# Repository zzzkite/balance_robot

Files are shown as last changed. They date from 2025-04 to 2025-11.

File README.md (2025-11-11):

# 轮腿机器人 - 毕设版

## PS2 操作说明

**注意：手柄信号可能不稳定，存在失控风险**

### 按键功能

- **失能按键**：`R2` (右上角第2个键)
  - 发送电机失能信号
  - 关节电机指示灯变为红色
  - 支持远程停止机器人

- **使能按键**：`start`
  - 发送电机使能信号  
  - 电机指示灯变为绿色

- **启动控制**：`L2` (左上角第二个键)
  - 需在电机使能后使用
  - 启动控制程序

- **跳跃功能**：`R1` (右上角第一个键)

- **前后移动**：右摇杆前后方向

- **左右旋转**：右摇杆左右方向

- **腿长变化**：左摇杆前后方向

- **横滚角控制**：左摇杆左右方向

## 项目文件架构
├── balance_robot_stm/ # STM32 主控代码
├── matlab/ # MATLAB 仿真文件
├── matlab results/ # 仿真视频和力矩数据
├── motor param/ # 关节电机参数存档
├── reference/ # 参考资料文档
├── Soildworks/ # 机械设计文件
│ ├── 3D模型/
│ ├── 打印件/
│ └── 机加工件/
├── test movie/ #实机测试视频
└── bom表/ # 物料清单

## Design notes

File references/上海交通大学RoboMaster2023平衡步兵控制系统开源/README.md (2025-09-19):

# 上海交通大学交龙战队平衡步兵控制系统开源说明文档

## 概述

本文档为上海交通大学交龙战队平衡步兵控制系统开源说明文档，给出了开源内容的索引和研发思路。本次开源的内容主要为控制系统的设计文档以及一些用于参考的测试视频。

本开源项目出自上海交通大学交龙战队，仅用于技术交流，未经作者允许，不得作任何商业用途。

转载需注明作品出处，对非法转载者，作者保留采用法律手段追究的权利。

## 索引

### 文档

1. 动力学模型-[WBR_control](WBR_control.html)
2. 腿部机构分析-[WBR_leg](WBR_leg.html)
3. 控制器设计-[WBR_control](WBR_control.html)

### 研发计划

1. 研发计划文档-[plan](plan.md)

### 手写稿

部分内容未整理成电子版，以手写稿形式开源，包括功率限制、自适应调节（防打滑策略）、陀螺平移等。此外建模分析和控制部分的电子稿在整理过程中可能有一些遗漏，手写稿也可作为一定参考。

1. 建模分析-[modelling](note/modelling/modeling_1.jpg)
2. 腿部机构分析-[leg](note/leg/leg_1.jpg)
3. 功率限制-[power](note/power/power_1.jpg)
4. 自适应调节-[predictor](note/predictor_and_controller.jpg)
5. 陀螺平移&腿部自重系数-[other](note/other.jpg)

### 控制系统框图

给出控制系统核心部分（运动控制-平衡、移动、旋转，腿部控制-高度、横滚）控制框图。系统由4部分组成：(1)目标状态输入，(2)控制器，(3)机器人模型，(4)观测器。

1. 系统框图-[system](assets/control_system/system.jpg)
2. 控制器-[controller](assets/control_system/controller.jpg)
3. 运动控制器-[locomotion_controller](assets/control_system/locomotion_controller.jpg)
4. 腿部控制器-[leg_controller](assets/control_system/leg_controller.jpg)
5. 观测器-[observer](assets/control_system/observer.jpg)

### 仿真

assets/sim_WBR_control 文件夹包含simulink仿真视频和仿真的状态曲线

### 测试视频

assets/test_video 文件夹中包含各项功能的测试视频，可作为运动性能和鲁棒性的参考。

## 硬件方案

- 驱动轮：3508电机+自制行星减速箱（14:1减速比）
- 关节电机：HT04
- 主控：STM32F407（C型开发板）
- IMU：BMI088（C板集成）

## 研发思路

我们的平衡步兵采用轮腿设计，轮腿结构在起伏路段、斜坡、横向移动等方面均有一定优势，相应的控制系统也相对复杂。考虑到模型的复杂性以及在单片机上运行的资源消耗等因素，采用LQR实现平衡运动控制。

2022赛季哈尔滨工程大学创梦之翼战队的平衡步兵在比赛中表现出了非常优秀的性能，赛季结束后他们也开源了平衡步兵的控制系统[1]。我们的控制系统在设计时一些处理参考了其思路。

此前轮腿机器人的模型多数简化为两级倒立摆[1][2][3]，对于两条腿的处理并不完善，同时轮电机的控制分为平衡移动和旋转两部分，不完全解耦。由此我们认为轮腿机器人在高速移动中的转向性能仍没有被完全发挥，因此在根据倒立摆模型初步验证了平衡控制算法后，重新建立了包含双腿的机器人全身动力学模型，并基于该模型设计了解耦的控制系统。

在完成核心的平衡、运动控制和腿部控制后，为了进一步提升平衡步兵在赛场上的性能和鲁棒性，我们又做了一系列优化和功能开发。

针对赛场上满地弹丸的场景设计了自适应调节器，设计该调节器的基本思路依然是希望控制输出解耦。相比根据额外的传感器判断是否踩到弹丸或轮子悬空，这种调节器不会破坏原有模型和控制系统的完整性，而是通过类似于轨迹跟踪的方式，仅在系统偏离模型的状态下介入，保证了系统的鲁棒性。

相比传统的四轮步兵，平衡车的功率限制相对难实现，也有采用超级电容+开环的做法，但一方面这样在电容没电时很容易超功率（赛场上不少队伍出现平衡卡墙后连续超功率的情况），另一方面也难以充分发挥平衡车的运动性能。平衡车功率限制的方式目前有两种：一种是采用NMPC控制，利用NMPC带约束优化的特性对功率进行限制（可参考广东工业大学DynamicX战队23赛季青工会答辩[4]），这种方式思路相对直观，但对计算平台算力要求很高；另一种方式是通过分析控制律，得到计算消耗非常低的功率限制条件，可在单片机上以1Khz运行。

由于平衡步兵无法实现全向移动，在赛场上操作存在许多制约。但在陀螺状态下，通过变速平衡车可以近似实现全向平移，这一功能在赛场上能有效提升平衡的机动性和生存能力。

最后，车的稳定性在比赛中尤为重要，平衡车具备在发生冲撞、下台阶、跳跃等情况时保持不翻，并在极短时间恢复平衡的能力才能支持操作手放心地完成各种操作。

## 参考资料

[1] [RoboMaster平衡步兵机器人控制系统设计](https://zhuanlan.zhihu.com/p/563048952)（哈尔滨工程大学创梦之翼战队，2022）  
[2] S. Wang et al., "Balance Control of a Novel Wheel-legged Robot: Design and Experiments," 2021 IEEE International Conference on Robotics and Automation (ICRA), 2021, pp. 6782-6788, doi: 10.1109/ICRA48506.2021.9561579.  
[3] V. Klemm et al., "Ascento: A Two-Wheeled Jumping Robot," 2019 International Conference on Robotics and Automation (ICRA), 2019, pp. 7515-7521, doi: 10.1109/ICRA.2019.8793792.  
[4] [RMUC 2023青工会技术答辩-广东工业大学-无下位机电控、平衡步兵模型预测控制](https://www.bilibili.com/video/BV18F41117QZ)

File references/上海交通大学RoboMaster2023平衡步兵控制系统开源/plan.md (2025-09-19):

# 轮腿平衡控制研发计划

## 1 基础平衡控制

固定腿长，平地直线运动，平衡控制基本原理验证

- [x] 动力学分析
- [x] 控制算法
- [x] 简化模型仿真验证
- [x] 腿部连杆运动学分析
- [x] 平衡+腿部控制仿真验证
- [ ] ~~非线性控制*~~

## 2 整体运动控制

实现基本的运动功能，优化运动性能

~~路线1~~

- [ ] 双腿协调
- [ ] 腿长控制
- [ ] 转向控制
- [ ] 横滚角

路线2（完整模型）

- [x] 全身动力学建模
- [x] 控制算法
- [x] 仿真验证

## 3 实际机器人控制

- [x] 无线调试器+串口测试
- [x] 陀螺仪校准
- [x] 线路连接设计
- [x] 关节电机驱动
- [x] 电机力控实现+验证
- [x] 腿部运动学验证
- [x] 控制算法实现
- [x] 测试

## 4 进阶功能

提升鲁棒性，实现一些进阶功能如跳跃、扰动自适应等。

- [x] 原地静止（尝试增大速度环系数+速度环输入限幅缩小+减小角度系数，效果不好则尝试力位混控）
- [x] 测试不同腿长起身效果，大角度状态缩短腿长
- [x] 扰动观测器
- [x] 打滑检测（观测器+力位混控）
- [x] 离地检测+落地（通过腿长PID输出可估计地面支持力，roll PID系数表示为腿长PID的函数）
- [x] 陀螺平移（偏心旋转，周期速度规划）
- [x] 主动跳跃（运动中跳跃/原地）
- [ ] 自动跳跃运动规划
- [x] 功率限制
- [x] 测试

## 5 整车

比赛用车整备至上场状态

硬件

- [x] 走线整理
- [x] 滑环焊线
- [x] 云台
- [x] 轮电机id+换线
- [x] minipc
- [x] 相机
- [x] 裁判系统
- [x] 电容
- [x] 继电器
- [x] 保护
- [x] 保养+备件

软件

- [x] 上板程序
- [x] 云台程序
- [x] 遥控器操作
- [x] 键鼠操作
- [x] 自瞄
- [x] 功率限制
- [ ] ui

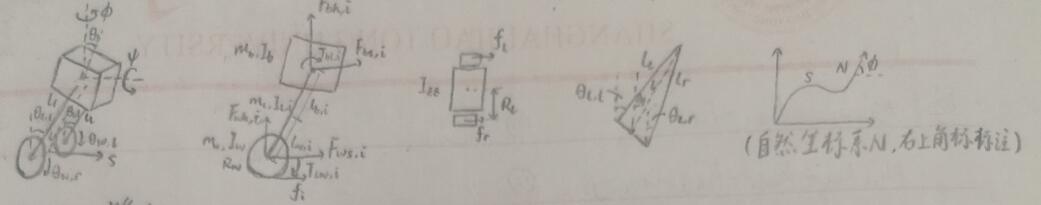
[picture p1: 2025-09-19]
references/上海交通大学RoboMaster2023平衡步兵控制系统开源/assets/figure/model.jpg

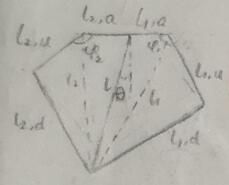
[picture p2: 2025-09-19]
references/上海交通大学RoboMaster2023平衡步兵控制系统开源/assets/figure/leg_1.jpg

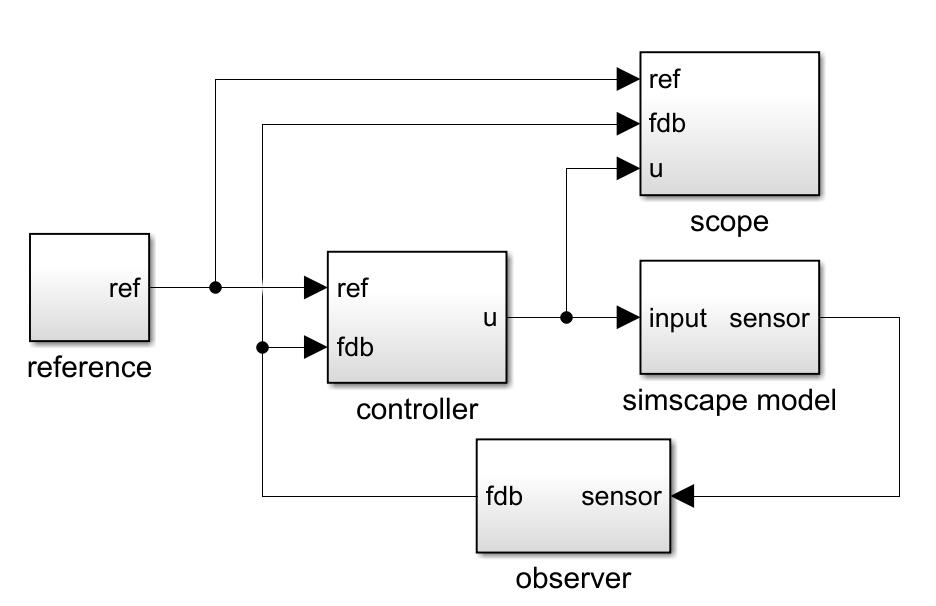
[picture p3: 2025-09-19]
references/上海交通大学RoboMaster2023平衡步兵控制系统开源/assets/control_system/system.jpg

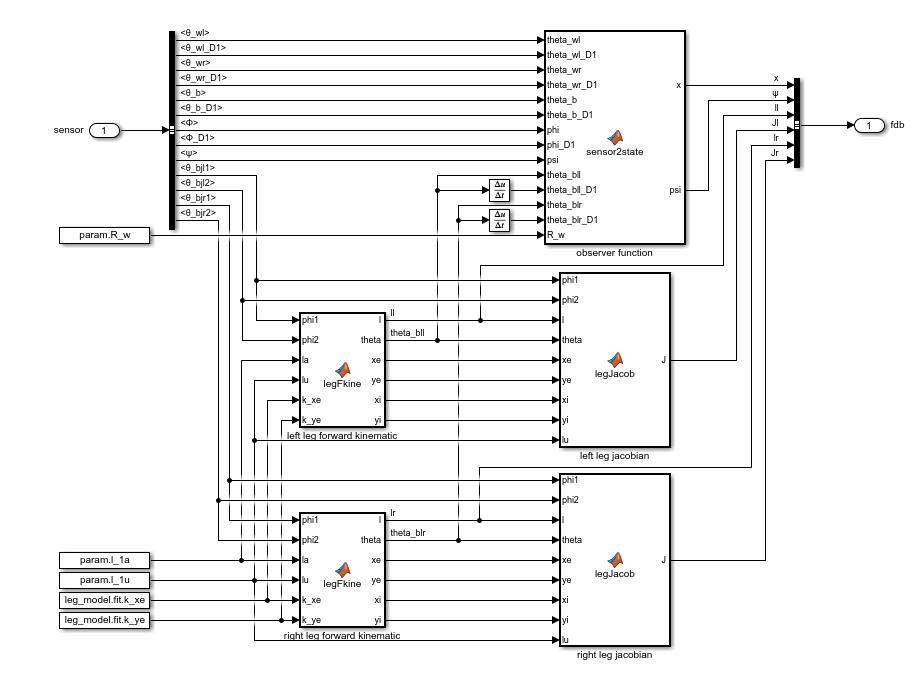
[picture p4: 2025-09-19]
references/上海交通大学RoboMaster2023平衡步兵控制系统开源/assets/control_system/observer.jpg

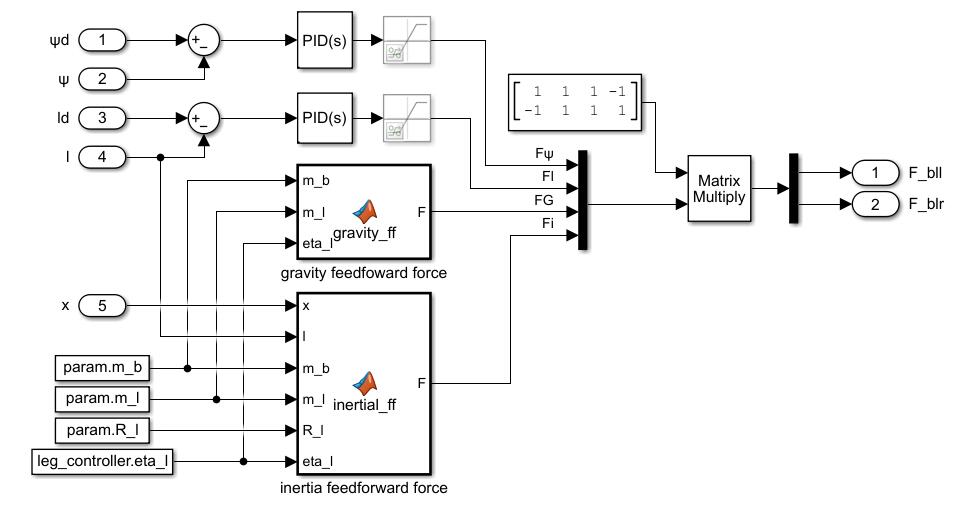
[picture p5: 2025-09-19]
references/上海交通大学RoboMaster2023平衡步兵控制系统开源/assets/control_system/leg_controller.jpg

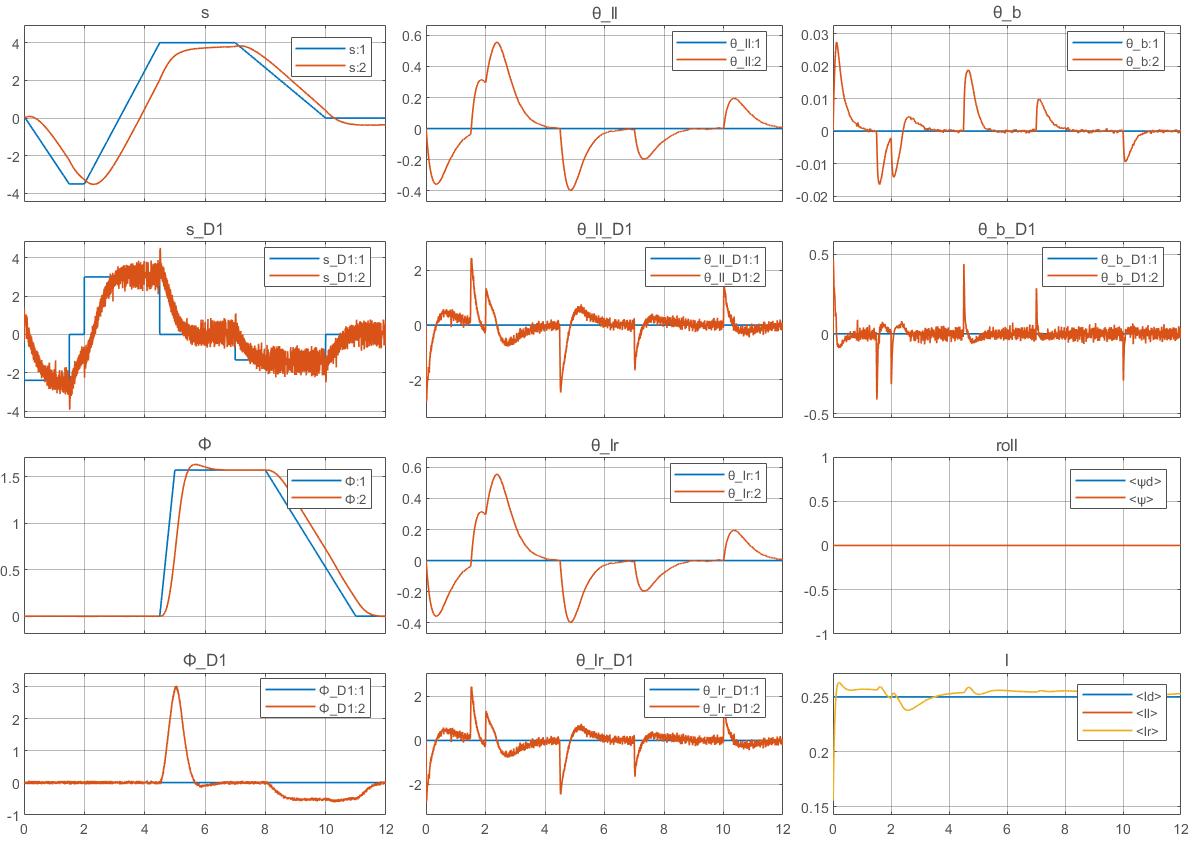
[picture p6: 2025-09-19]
references/上海交通大学RoboMaster2023平衡步兵控制系统开源/assets/sim_WBR_control/state.jpg

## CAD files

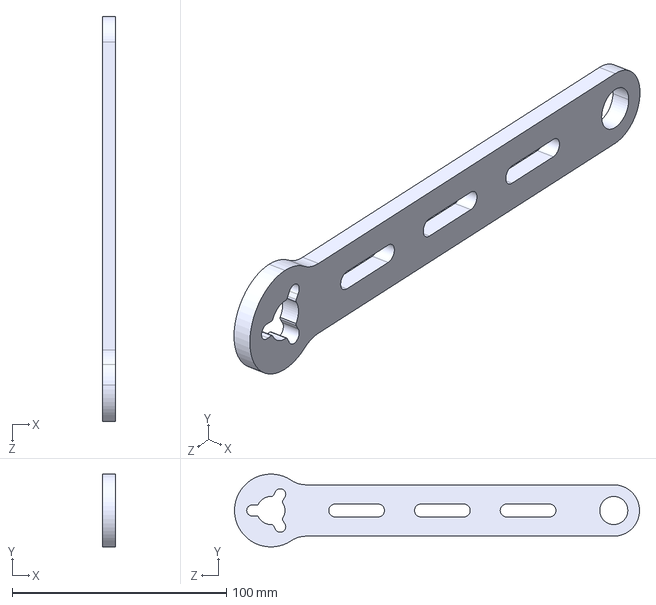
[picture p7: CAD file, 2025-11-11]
Soildworks/Version1.0-sw-加工件/加工连杆2.STEP
6.00 x 34.0 x 189.0 mm

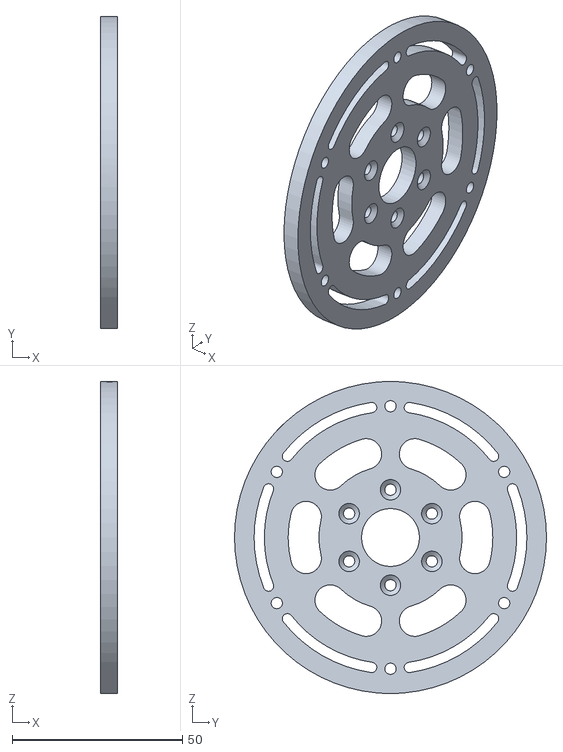
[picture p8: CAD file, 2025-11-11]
Soildworks/Version1.0-sw-打印件/轮毂打印件-上盖片.STL
5.00 x 91.5 x 91.5

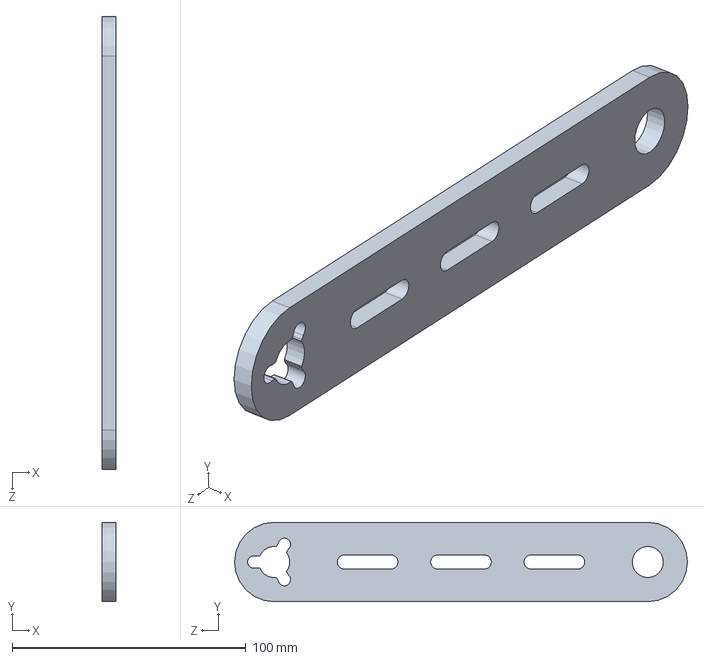
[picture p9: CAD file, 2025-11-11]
Soildworks/Version1.0-sw/连杆6.sldprt
6.00 x 34.0 x 194.0 mm

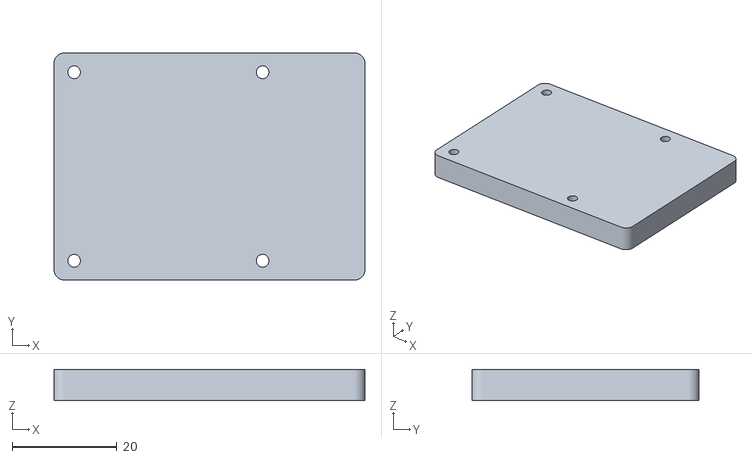
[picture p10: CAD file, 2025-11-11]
Soildworks/Version1.0-sw-打印件/stm32后壳.STL
59.4 x 43.4 x 6.00

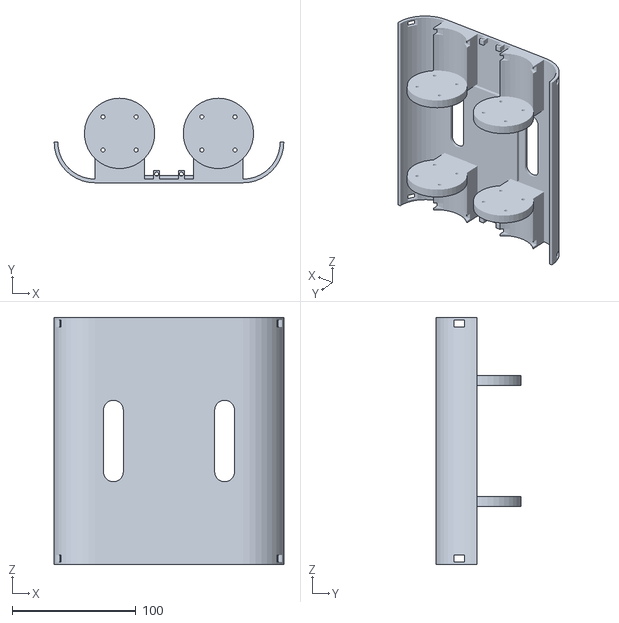
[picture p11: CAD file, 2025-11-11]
Soildworks/Version1.0-sw-打印件/机架底板.STL
186.0 x 68.5 x 200.0

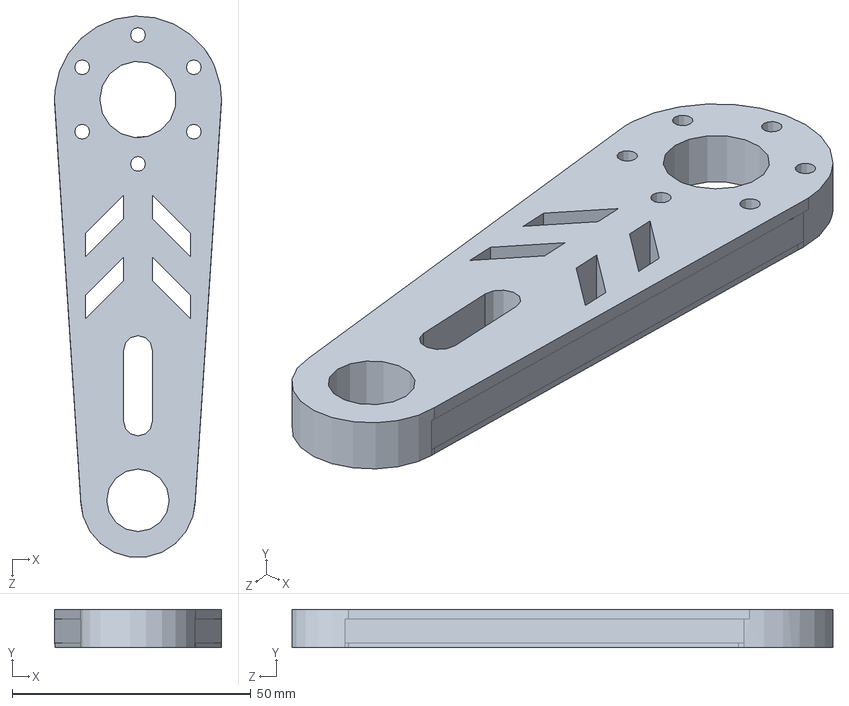
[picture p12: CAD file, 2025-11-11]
Soildworks/Version1.0-sw/加工连杆3.sldprt
35.0 x 8.00 x 113.4 mm

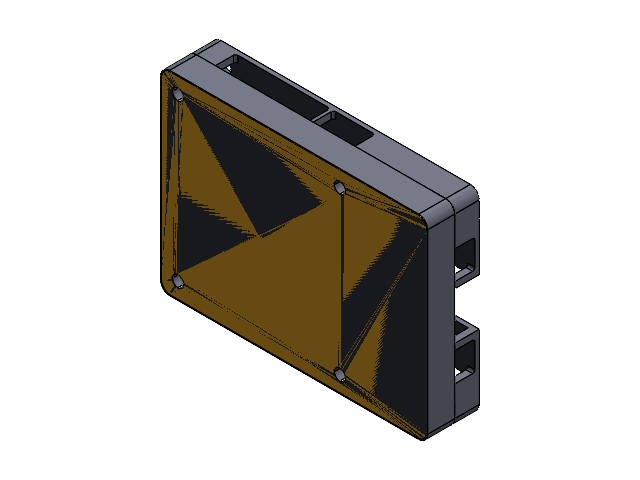
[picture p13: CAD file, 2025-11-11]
Soildworks/Version1.0-sw/stm32装配体.SLDASM
stm32后壳
stm32前壳

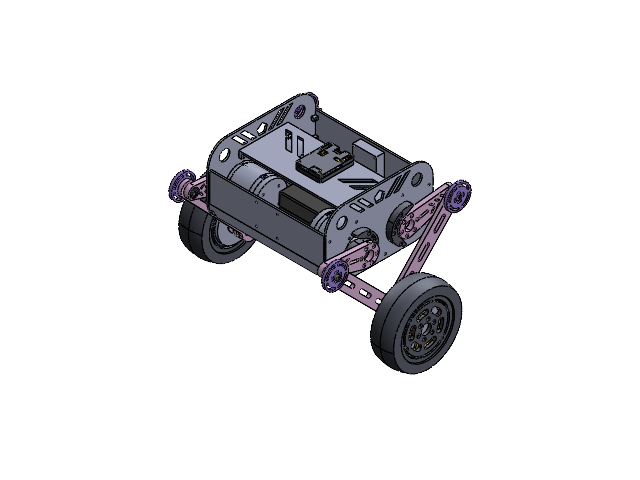
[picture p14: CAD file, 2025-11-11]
Soildworks/Version1.0-sw/总装.SLDASM
连杆4 x 2
连杆3 x 2
电机连接打印件-1 x 2
5-13-4法兰轴承 x 20
垫片-m5-8-0_5 x 10
连杆1 x 2
支撑轮 x 4
连杆2 x 2
沉头螺丝-m3_10 x 4
5x2实心轮胎 x 2
轮毂打印件-内圈 x 2
轮毂打印件-上盖片 x 2
杯头螺丝-m3_40 x 2
6215_轮毂电机3D模型20240821 x 2
轮毂打印垫片 x 2
m3螺母 x 2
轮毂打印件-下盖片 x 2
杯头螺丝-m5_25 x 4
stm32后壳
stm32前壳
E626S电池..图）
机架底板
机架侧板 x 2
机架垫高层
机架前板 x 2
DM-J4310-2EC-V1.1__3d_20240822_1 x 4
电机连接打印件-2 x 4
RM分电板
挡块-1 x 2
挡块-2 x 2
导轮架
导轮

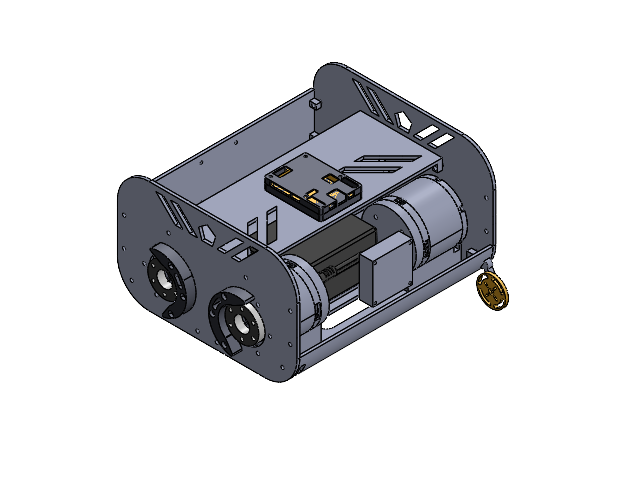
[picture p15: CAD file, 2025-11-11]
Soildworks/Version1.0-sw/机架装配体.SLDASM
stm32后壳
stm32前壳
E626S电池..图）
机架底板
机架侧板 x 2
机架垫高层
机架前板
DM-J4310-2EC-V1.1__3d_20240822_1 x 4
电机连接打印件-2 x 4
RM分电板
挡块-1 x 2
挡块-2 x 2
导轮架
导轮

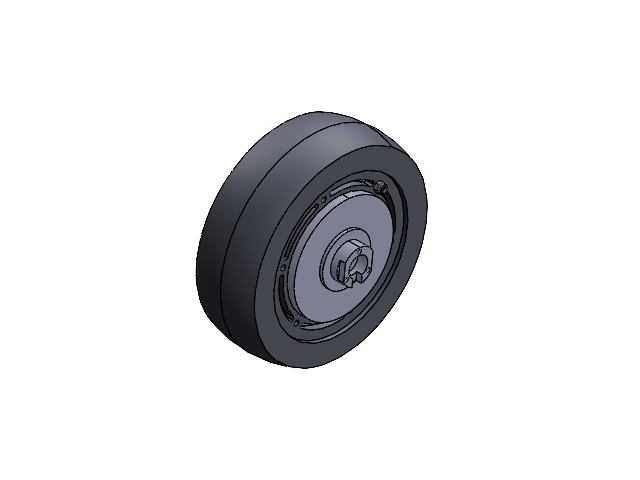
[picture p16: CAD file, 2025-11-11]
Soildworks/Version1.0-sw/轮装配体.SLDASM
5x2实心轮胎
轮毂打印件-内圈
轮毂打印件-上盖片
杯头螺丝-m3_40
6215_轮毂电机3D模型20240821
轮毂打印垫片
沉头螺丝-m3_10
m3螺母
轮毂打印件-下盖片

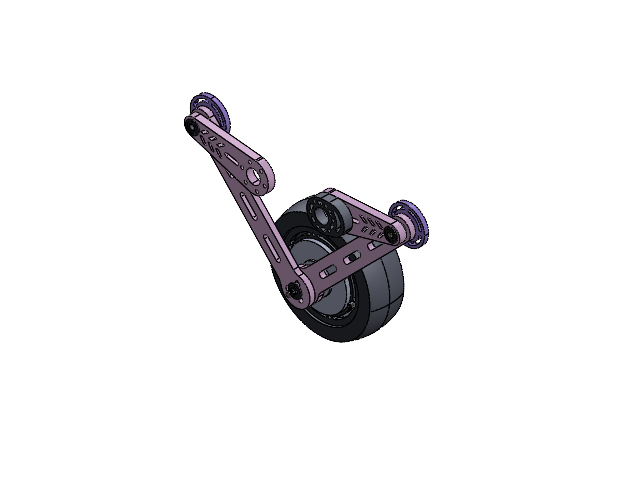
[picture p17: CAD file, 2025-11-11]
Soildworks/Version1.0-sw/腿装配体.SLDASM
连杆4
连杆3
电机连接打印件-1
5-13-4法兰轴承 x 10
垫片-m5-8-0_5 x 5
连杆1
支撑轮 x 2
连杆2
沉头螺丝-m3_10 x 2
5x2实心轮胎
轮毂打印件-内圈
轮毂打印件-上盖片
杯头螺丝-m3_40
6215_轮毂电机3D模型20240821
轮毂打印垫片
m3螺母
轮毂打印件-下盖片
杯头螺丝-m5_25 x 2

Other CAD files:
Soildworks/Version1.0-sw-加工件/连杆1.STEP
Soildworks/Version1.0-sw/加工连杆2.sldprt
Soildworks/Version1.0-sw-加工件/连杆2.STEP
Soildworks/Version1.0-sw/stm32后壳.sldprt
Soildworks/Version1.0-sw-加工件/加工连杆1.STEP
Soildworks/Version1.0-sw-打印件/连杆2.STL
Soildworks/Version1.0-sw-加工件/加工连杆3.STEP
Soildworks/Version1.0-sw-打印件/stm32前壳.STL
Soildworks/Version1.0-sw-打印件/导轮.STL
Soildworks/Version1.0-sw-打印件/导轮架.STL
Soildworks/Version1.0-sw-打印件/挡块-1.STL
Soildworks/Version1.0-sw-打印件/挡块-2.STL
Soildworks/Version1.0-sw-打印件/支撑轮.STL
Soildworks/Version1.0-sw-打印件/机架侧板.STL
Soildworks/Version1.0-sw-打印件/机架前板.STL
Soildworks/Version1.0-sw-打印件/机架垫高层.STL
Soildworks/Version1.0-sw-打印件/电机连接打印件-1.STL
Soildworks/Version1.0-sw-打印件/电机连接打印件-2.STL
Soildworks/Version1.0-sw-打印件/轮毂打印件-下盖片.STL
Soildworks/Version1.0-sw-打印件/轮毂打印件-内圈.STL
Soildworks/Version1.0-sw-打印件/轮毂打印垫片.STL
Soildworks/Version1.0-sw-打印件/连杆1.STL
Soildworks/Version1.0-sw-打印件/连杆3.STL
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

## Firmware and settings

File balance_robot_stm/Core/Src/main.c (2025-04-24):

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
/* Includes ------------------------------------------------------------------*/
#include "main.h"
#include "cmsis_os.h"
#include "dma.h"
#include "fdcan.h"
#include "memorymap.h"
#include "spi.h"
#include "tim.h"
#include "gpio.h"

/* USER CODE BEGIN Includes */
#include "bsp_can.h"
#include "bsp_dwt.h"
#include "BMI088driver.h"
#include "BMI088Middleware.h"
#include "Motor.h"
/* USER CODE END Includes */


void SystemClock_Config(void);
void PeriphCommonClock_Config(void);
void MX_FREERTOS_Init(void);
/**
  * @brief  The application entry point.
  * @retval int
  */
int main(void)
{

  /* MCU Configuration--------------------------------------------------------*/

  /* Reset of all peripherals, Initializes the Flash interface and the Systick. */
  HAL_Init();

  /* Configure the system clock */
  SystemClock_Config();

  /* Configure the peripherals common clocks */
  PeriphCommonClock_Config();

  /* Initialize all configured peripherals */

  MX_GPIO_Init();
  MX_DMA_Init();
  MX_FDCAN1_Init();
  MX_SPI2_Init();
  MX_FDCAN2_Init();
  MX_FDCAN3_Init();
  MX_TIM3_Init();
  /* USER CODE BEGIN 2 */
	DWT_Init(480); 
	HAL_TIM_PWM_Start(&htim3, TIM_CHANNEL_4);
	while (BMI088_init(&hspi2, 0) != BMI088_NO_ERROR) // 0为不校准，1为进入校准模式
	{
	  ;
	}
	BSP_FDCAN1_Init(); //start fdcan and fifo
	BSP_FDCAN2_Init();
	Power_OUT1_ON;
	Power_OUT2_ON;
  /* USER CODE END 2 */

  /* Call init function for freertos objects (in cmsis_os2.c) */
  MX_FREERTOS_Init();

  /* Start scheduler */
  osKernelStart();

  /* We should never get here as control is now taken by the scheduler */

  /* Infinite loop */
  /* USER CODE BEGIN WHILE */
  while (1)
  {
    /* USER CODE END WHILE */

    /* USER CODE BEGIN 3 */
  }
  /* USER CODE END 3 */
}

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
/**
  * @brief  Period elapsed callback in non blocking mode
  * @note   This function is called  when TIM2 interrupt took place, inside
  * HAL_TIM_IRQHandler(). It makes a direct call to HAL_IncTick() to increment
  * a global variable "uwTick" used as application time base.
  * @param  htim : TIM handle
  * @retval None
  */
void HAL_TIM_PeriodElapsedCallback(TIM_HandleTypeDef *htim)
{
  if (htim->Instance == TIM2)
  {
    HAL_IncTick();
  }
}

/**
  * @brief  This function is executed in case of error occurrence.
  * @retval None
  */
void Error_Handler(void)
{
  /* USER CODE BEGIN Error_Handler_Debug */
  /* User can add his own implementation to report the HAL error return state */
  __disable_irq();
  while (1)
  {
  }
  /* USER CODE END Error_Handler_Debug */
}

#ifdef  USE_FULL_ASSERT
/**
  * @brief  Reports the name of the source file and the source line number
  *         where the assert_param error has occurred.
  * @param  file: pointer to the source file name
  * @param  line: assert_param error line source number
  * @retval None
  */
void assert_failed(uint8_t *file, uint32_t line)
{
  /* USER CODE BEGIN 6 */
  /* User can add his own implementation to report the file name and line number,
     ex: printf("Wrong parameters value: file %s on line %d\r\n", file, line) */
  /* USER CODE END 6 */
}
#endif /* USE_FULL_ASSERT */

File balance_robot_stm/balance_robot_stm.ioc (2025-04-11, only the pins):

Mcu.UserName=STM32H723VGTx
PA0.GPIO_Label=DI
PA0.Signal=GPIO_Input
PA13(JTMS/SWDIO).Signal=DEBUG_JTMS-SWDIO
PA14(JTCK/SWCLK).Signal=DEBUG_JTCK-SWCLK
PA2.GPIO_Label=DO
PA2.Signal=GPIO_Output
PB1.Signal=S_TIM3_CH4
PB13.Signal=SPI2_SCK
PB5.Signal=FDCAN2_RX
PB6.Signal=FDCAN2_TX
PC0.GPIO_Label=ACC_CS
PC0.Signal=GPIO_Output
PC1.Signal=SPI2_MOSI
PC13.Signal=GPIO_Output
PC14-OSC32_IN.Signal=GPIO_Output
PC2_C.Signal=SPI2_MISO
PC3_C.GPIO_Label=GYRO_CS
PC3_C.Signal=GPIO_Output
PD0.Signal=FDCAN1_RX
PD1.Signal=FDCAN1_TX
PD12.Signal=FDCAN3_RX
PD13.Signal=FDCAN3_TX
PE10.GPIO_Label=ACC_INT
PE10.Signal=GPXTI10
PE12.GPIO_Label=GYRO_INT
PE12.Signal=GPXTI12
PE13.GPIO_Label=CLK
PE13.Signal=GPIO_Output
PE9.GPIO_Label=CS
PE9.Signal=GPIO_Output
PH0-OSC_IN.Signal=RCC_OSC_IN
PH1-OSC_OUT.Signal=RCC_OSC_OUT

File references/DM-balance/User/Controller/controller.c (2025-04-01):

/**
 ******************************************************************************
 * @file    controller.c
 * @author  Wang Hongxi
 * @author  Zhang Hongyu (fuzzy pid)
 * @version V1.1.3
 * @date    2021/7/3
 * @brief   DWT定时器用于计算控制周期，OLS用于提取信号微分
 ******************************************************************************
 * @attention
 *
 ******************************************************************************
 */
#include "controller.h"

/******************************** FUZZY PID **********************************/
static float FuzzyRuleKpRAW[7][7] = {
    PB, PB, PM, PM, PS, ZE, ZE,
    PB, PB, PM, PS, PS, ZE, PS,
    PM, PM, PM, PS, ZE, PS, PS,
    PM, PM, PS, ZE, PS, PM, PM,
    PS, PS, ZE, PS, PS, PM, PM,
    PS, ZE, PS, PM, PM, PM, PB,
    ZE, ZE, PM, PM, PM, PB, PB};

static float FuzzyRuleKiRAW[7][7] = {
    PB, PB, PM, PM, PS, ZE, ZE,
    PB, PB, PM, PS, PS, ZE, ZE,
    PB, PM, PM, PS, ZE, PS, PS,
    PM, PM, PS, ZE, PS, PM, PM,
    PS, PS, ZE, PS, PS, PM, PB,
    ZE, ZE, PS, PS, PM, PB, PB,
    ZE, ZE, PS, PM, PM, PB, PB};

static float FuzzyRuleKdRAW[7][7] = {
    PS, PS, PB, PB, PB, PM, PS,
    PS, PS, PB, PM, PM, PS, ZE,
    ZE, PS, PM, PM, PS, PS, ZE,
    ZE, PS, PS, PS, PS, PS, ZE,
    ZE, ZE, ZE, ZE, ZE, ZE, ZE,
    PB, PS, PS, PS, PS, PS, PB,
    PB, PM, PM, PM, PS, PS, PB};

void Fuzzy_Rule_Init(FuzzyRule_t *fuzzyRule, float (*fuzzyRuleKp)[7], float (*fuzzyRuleKi)[7], float (*fuzzyRuleKd)[7],
                     float kpRatio, float kiRatio, float kdRatio,
                     float eStep, float ecStep)
{
    if (fuzzyRuleKp == NULL)
        fuzzyRule->FuzzyRuleKp = FuzzyRuleKpRAW;
    else
        fuzzyRule->FuzzyRuleKp = fuzzyRuleKp;
    if (fuzzyRuleKi == NULL)
        fuzzyRule->FuzzyRuleKi = FuzzyRuleKiRAW;
    else
        fuzzyRule->FuzzyRuleKi = fuzzyRuleKi;
    if (fuzzyRuleKd == NULL)
        fuzzyRule->FuzzyRuleKd = FuzzyRuleKdRAW;
    else
        fuzzyRule->FuzzyRuleKd = fuzzyRuleKd;

    fuzzyRule->KpRatio = kpRatio;
    fuzzyRule->KiRatio = kiRatio;
    fuzzyRule->KdRatio = kdRatio;

    if (eStep < 0.00001f)
        eStep = 1;
    if (ecStep < 0.00001f)
        ecStep = 1;
    fuzzyRule->eStep = eStep;
    fuzzyRule->ecStep = ecStep;
}
void Fuzzy_Rule_Implementation(FuzzyRule_t *fuzzyRule, float measure, float ref)
{
    float eLeftTemp, ecLeftTemp;
    float eRightTemp, ecRightTemp;
    int eLeftIndex, ecLeftIndex;
    int eRightIndex, ecRightIndex;

    fuzzyRule->dt = DWT_GetDeltaT((void *)fuzzyRule->DWT_CNT);

    fuzzyRule->e = ref - measure;
    fuzzyRule->ec = (fuzzyRule->e - fuzzyRule->eLast) / fuzzyRule->dt;
    fuzzyRule->eLast = fuzzyRule->e;

    //隶属区间
    eLeftIndex = fuzzyRule->e >= 3 * fuzzyRule->eStep ? 6 : (fuzzyRule->e <= -3 * fuzzyRule->eStep ? 0 : (fuzzyRule->e >= 0 ? ((int)(fuzzyRule->e / fuzzyRule->eStep) + 3) : ((int)(fuzzyRule->e / fuzzyRule->eStep) + 2)));
    eRightIndex = fuzzyRule->e >= 3 * fuzzyRule->eStep ? 6 : (fuzzyRule->e <= -3 * fuzzyRule->eStep ? 0 : (fuzzyRule->e >= 0 ? ((int)(fuzzyRule->e / fuzzyRule->eStep) + 4) : ((int)(fuzzyRule->e / fuzzyRule->eStep) + 3)));
    ecLeftIndex = fuzzyRule->ec >= 3 * fuzzyRule->ecStep ? 6 : (fuzzyRule->ec <= -3 * fuzzyRule->ecStep ? 0 : (fuzzyRule->ec >= 0 ? ((int)(fuzzyRule->ec / fuzzyRule->ecStep) + 3) : ((int)(fuzzyRule->ec / fuzzyRule->ecStep) + 2)));
    ecRightIndex = fuzzyRule->ec >= 3 * fuzzyRule->ecStep ? 6 : (fuzzyRule->ec <= -3 * fuzzyRule->ecStep ? 0 : (fuzzyRule->ec >= 0 ? ((int)(fuzzyRule->ec / fuzzyRule->ecStep) + 4) : ((int)(fuzzyRule->ec / fuzzyRule->ecStep) + 3)));

    //隶属度
    eLeftTemp = fuzzyRule->e >= 3 * fuzzyRule->eStep ? 0 : (fuzzyRule->e <= -3 * fuzzyRule->eStep ? 1 : (eRightIndex - fuzzyRule->e / fuzzyRule->eStep - 3));
    eRightTemp = fuzzyRule->e >= 3 * fuzzyRule->eStep ? 1 : (fuzzyRule->e <= -3 * fuzzyRule->eStep ? 0 : (fuzzyRule->e / fuzzyRule->eStep - eLeftIndex + 3));
    ecLeftTemp = fuzzyRule->ec >= 3 * fuzzyRule->ecStep ? 0 : (fuzzyRule->ec <= -3 * fuzzyRule->ecStep ? 1 : (ecRightIndex - fuzzyRule->ec / fuzzyRule->ecStep - 3));
    ecRightTemp = fuzzyRule->ec >= 3 * fuzzyRule->ecStep ? 1 : (fuzzyRule->ec <= -3 * fuzzyRule->ecStep ? 0 : (fuzzyRule->ec / fuzzyRule->ecStep - ecLeftIndex + 3));

    fuzzyRule->KpFuzzy = eLeftTemp * ecLeftTemp * fuzzyRule->FuzzyRuleKp[eLeftIndex][ecLeftIndex] +
                         eLeftTemp * ecRightTemp * fuzzyRule->FuzzyRuleKp[eRightIndex][ecLeftIndex] +
                         eRightTemp * ecLeftTemp * fuzzyRule->FuzzyRuleKp[eLeftIndex][ecRightIndex] +
                         eRightTemp * ecRightTemp * fuzzyRule->FuzzyRuleKp[eRightIndex][ecRightIndex];

    fuzzyRule->KiFuzzy = eLeftTemp * ecLeftTemp * fuzzyRule->FuzzyRuleKi[eLeftIndex][ecLeftIndex] +
                         eLeftTemp * ecRightTemp * fuzzyRule->FuzzyRuleKi[eRightIndex][ecLeftIndex] +
                         eRightTemp * ecLeftTemp * fuzzyRule->FuzzyRuleKi[eLeftIndex][ecRightIndex] +
                         eRightTemp * ecRightTemp * fuzzyRule->FuzzyRuleKi[eRightIndex][ecRightIndex];

    fuzzyRule->KdFuzzy = eLeftTemp * ecLeftTemp * fuzzyRule->FuzzyRuleKd[eLeftIndex][ecLeftIndex] +
                         eLeftTemp * ecRightTemp * fuzzyRule->FuzzyRuleKd[eRightIndex][ecLeftIndex] +
                         eRightTemp * ecLeftTemp * fuzzyRule->FuzzyRuleKd[eLeftIndex][ecRightIndex] +
                         eRightTemp * ecRightTemp * fuzzyRule->FuzzyRuleKd[eRightIndex][ecRightIndex];
}

/******************************* PID CONTROL *********************************/
// PID优化环节函数声明
static void f_Trapezoid_Intergral(PID_t *pid);
static void f_Integral_Limit(PID_t *pid);
static void f_Derivative_On_Measurement(PID_t *pid);
static void f_Changing_Integration_Rate(PID_t *pid);
static void f_Output_Filter(PID_t *pid);
static void f_Derivative_Filter(PID_t *pid);
static void f_Output_Limit(PID_t *pid);
static void f_Proportion_Limit(PID_t *pid);
static void f_PID_ErrorHandle(PID_t *pid);
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

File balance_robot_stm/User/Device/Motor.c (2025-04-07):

#include "Motor.h"

// CAN1
DM_Motor_Info_Typedef DM_4310_Motor_leftfront = {
 
	 .CANFrameInfo = {
		.CAN_ID = 0x08, 
	  .Master_ID = 0x04, 
	 },
};

DM_Motor_Info_Typedef DM_4310_Motor_leftback = {
 
	 .CANFrameInfo = {
		.CAN_ID = 0x06, 
	  .Master_ID = 0x03, 
	 },
};

DM_Motor_Info_Typedef DM_6215_Motor_left = {
 
	 .CANFrameInfo = {
		.CAN_ID = 0x01, 
	  .Master_ID = 0x00, 
	 },
};

// CAN2
DM_Motor_Info_Typedef DM_4310_Motor_rightfront = {
 
	 .CANFrameInfo = {
		.CAN_ID = 0x06, 
	  .Master_ID = 0x03, 
	 },
};

DM_Motor_Info_Typedef DM_4310_Motor_rightback = {
 
	 .CANFrameInfo = {
		.CAN_ID = 0x08, 
	  .Master_ID = 0x04, 
	 },
};

DM_Motor_Info_Typedef DM_6215_Motor_right = {
 
	 .CANFrameInfo = {
		.CAN_ID = 0x01, 
	  .Master_ID = 0x00, 
	 },
};



DM_Motor_Control_Typedef DM_Motor_Control;

//uint -> float解码函数
//param: 原数据，映射范围min & max，位数
//以16位为例，x_int=32767时位于0点附近
static float uint_to_float(int X_int, float X_min, float X_max, int Bits){
    float span = X_max - X_min;
    float offset = X_min;
    return ((float)X_int)*span/((float)((1<<Bits)-1)) + offset;
}

//同上
static int float_to_uint(float X_float, float X_min, float X_max, int bits){
    float span = X_max - X_min;
    float offset = X_min;
    return (int) ((X_float-offset)*((float)((1<<bits)-1))/span);
}

// 控制帧函数
// param: CAN发送结构体地址，发送的CAN_ID，控制命令
// 奇怪的是这里CMD类型为DM_Motor_CMD_e会报错
void DM_Motor_Command(FDCAN_TxFrame_TypeDef *TxFrame,DM_Motor_Info_Typedef *DM_Motor ,uint8_t CMD){

	 TxFrame->Header.Identifier = DM_Motor->CANFrameInfo.CAN_ID;
  	
	 TxFrame->Data[0] = 0xFF;
   TxFrame->Data[1] = 0xFF;
 	 TxFrame->Data[2] = 0xFF;
	 TxFrame->Data[3] = 0xFF;
	 TxFrame->Data[4] = 0xFF;
	 TxFrame->Data[5] = 0xFF;
	 TxFrame->Data[6] = 0xFF;
	
	 switch(CMD){
		 
		  case Motor_Enable :
	        TxFrame->Data[7] = 0xFC; 
	    break;
      
			case Motor_Disable :
	        TxFrame->Data[7] = 0xFD; 
      break;
      
			case Motor_Save_Zero_Position :
	        TxFrame->Data[7] = 0xFE; 
			break;
			
			case DM_Motor_CMD_Type_Num :
					TxFrame->Data[7] = 0xFB;
			break;
			
			default:
	    break;   
	}
	
	// 发送
   HAL_FDCAN_AddMessageToTxFifoQ(TxFrame->hcan,&TxFrame->Header,TxFrame->Data);
}

// 获取系统参数
void DM_Motor_Read_Param(FDCAN_TxFrame_TypeDef *TxFrame,DM_Motor_Info_Typedef *DM_Motor,uint8_t RID){

   TxFrame->Header.Identifier = 0x7FF;
	 TxFrame->Data[0] = (uint8_t)(DM_Motor->CANFrameInfo.CAN_ID);
	 TxFrame->Data[1] = (uint8_t)(DM_Motor->CANFrameInfo.CAN_ID >> 8);
	 TxFrame->Data[2] = 0x33;
	 TxFrame->Data[3] = RID;
	 TxFrame->Data[4] = 0;
	 TxFrame->Data[5] = 0;
	 TxFrame->Data[6] = 0; 
	 TxFrame->Data[7] = 0;   
	 
 HAL_FDCAN_AddMessageToTxFifoQ(TxFrame->hcan,&TxFrame->Header,TxFrame->Data); 
}

// 写入系统参数
void DM_Motor_Write_Param(FDCAN_TxFrame_TypeDef *TxFrame,DM_Motor_Info_Typedef *DM_Motor,uint8_t RID,uint8_t *Write_Param){

   TxFrame->Header.Identifier = 0x7FF;
	 TxFrame->Data[0] = (uint8_t)(DM_Motor->CANFrameInfo.CAN_ID);
	 TxFrame->Data[1] = (uint8_t)(DM_Motor->CANFrameInfo.CAN_ID >> 8);
	 TxFrame->Data[2] = 0x55;
	 TxFrame->Data[3] = RID;
	 TxFrame->Data[4] = Write_Param[0];
	 TxFrame->Data[5] = Write_Param[1];
	 TxFrame->Data[6] = Write_Param[2]; 
	 TxFrame->Data[7] = Write_Param[3];   
	 
 HAL_FDCAN_AddMessageToTxFifoQ(TxFrame->hcan,&TxFrame->Header,TxFrame->Data); 
}

// 保存写入的系统参数
void DM_Motor_Save_Param(FDCAN_TxFrame_TypeDef *TxFrame,DM_Motor_Info_Typedef *DM_Motor){

   TxFrame->Header.Identifier = 0x7FF;
	 TxFrame->Data[0] = (uint8_t)(DM_Motor->CANFrameInfo.CAN_ID);
	 TxFrame->Data[1] = (uint8_t)(DM_Motor->CANFrameInfo.CAN_ID >> 8);
	 TxFrame->Data[2] = 0xAA;
	 TxFrame->Data[3] = 1;
	 TxFrame->Data[4] = 0;
	 TxFrame->Data[5] = 0;
	 TxFrame->Data[6] = 0; 
	 TxFrame->Data[7] = 0;   
	 
 HAL_FDCAN_AddMessageToTxFifoQ(TxFrame->hcan,&TxFrame->Header,TxFrame->Data); 
}

// 电机保护限幅，控制器中应该用等幅限制输出
static float DM_Motor_Limit_float(float input, float max)
{
	if(input > max)
		input = max;
	else if (input < -max)
		input = -max;
	return input;
}

// 4310电机控制
// param: Fdcan发送结构体，电机总结构体，电机模式，位置，速度，KP，KD，力矩
void DM_Motor_CAN_TxMessage_4310(FDCAN_TxFrame_TypeDef *TxFrame, DM_Motor_Info_Typedef *DM_Motor, uint8_t Mode, float Postion, float Velocity, float KP, float KD, float Torque){

	  if(Mode > Velocity_Mode) Mode = MIT_Mode; //只有3种模式，标识默认为MIT模式
	
		// MIT模式
	  if(Mode == MIT_Mode) {
		
			 static uint16_t Postion_Tmp,Velocity_Tmp,Torque_Tmp,KP_Tmp,KD_Tmp;
			 
			 //输出限幅：
			 Postion = DM_Motor_Limit_float(Postion, P_MAX_4310);
			 Velocity = DM_Motor_Limit_float(Velocity, V_MAX_4310);
			 Torque = DM_Motor_Limit_float(Torque, 3);
			
			 Postion_Tmp  =  float_to_uint(Postion,-P_MAX_4310,P_MAX_4310,16) ;
			 Velocity_Tmp =  float_to_uint(Velocity,-V_MAX_4310,V_MAX_4310,12);
			 Torque_Tmp = float_to_uint(Torque,-T_MAX_4310,T_MAX_4310,12);
			 KP_Tmp = float_to_uint(KP,0,500,12);
			 KD_Tmp = float_to_uint(KD,0,5,12);

			 TxFrame->Header.Identifier = DM_Motor->CANFrameInfo.CAN_ID;
			 
			 TxFrame->Data[0] = (uint8_t)(Postion_Tmp>>8);
			 TxFrame->Data[1] = (uint8_t)(Postion_Tmp);
			 TxFrame->Data[2] = (uint8_t)(Velocity_Tmp>>4);
			 TxFrame->Data[3] = (uint8_t)((Velocity_Tmp&0x0F)<<4) | (KP_Tmp>>8);
			 TxFrame->Data[4] = (uint8_t)(KP_Tmp);
			 TxFrame->Data[5] = (uint8_t)(KD_Tmp>>4);
			 TxFrame->Data[6] = (uint8_t)((KD_Tmp&0x0F)<<4) | (Torque_Tmp>>8);
			 TxFrame->Data[7] = (uint8_t)(Torque_Tmp);
			
			 HAL_FDCAN_AddMessageToTxFifoQ(TxFrame->hcan,&TxFrame->Header,TxFrame->Data);
	 
	 }else if(Mode == Position_Velocity_Mode){
	 
		   KP = 0; KD = 0; Torque = 0;
		 
       uint8_t *Postion_Tmp,*Velocity_Tmp;
		   
		   Postion_Tmp = (uint8_t *)&Postion; 
		   Velocity_Tmp = (uint8_t *)&Velocity; 
		 
	     TxFrame->Header.Identifier = DM_Motor->CANFrameInfo.CAN_ID + 0x100;
			 
			 TxFrame->Data[0] = *(Postion_Tmp);
			 TxFrame->Data[1] = *(Postion_Tmp + 1);
			 TxFrame->Data[2] = *(Postion_Tmp + 2);
			 TxFrame->Data[3] = *(Postion_Tmp + 3);
			 TxFrame->Data[4] = *(Velocity_Tmp);
			 TxFrame->Data[5] = *(Velocity_Tmp + 1);
			 TxFrame->Data[6] = *(Velocity_Tmp + 2);
			 TxFrame->Data[7] = *(Velocity_Tmp + 3);
			
			 HAL_FDCAN_AddMessageToTxFifoQ(TxFrame->hcan,&TxFrame->Header,TxFrame->Data);
	 
	 }else if(Mode == Velocity_Mode){
	 
	     Postion = 0;KP = 0; KD = 0; Torque = 0;
		 
       uint8_t *Velocity_Tmp;
		   
		   Velocity_Tmp = (uint8_t *)&Velocity; 
		 
	     TxFrame->Header.Identifier = DM_Motor->CANFrameInfo.CAN_ID + 0x200;
			 
			 TxFrame->Data[0] = *(Velocity_Tmp);
			 TxFrame->Data[1] = *(Velocity_Tmp + 1);
			 TxFrame->Data[2] = *(Velocity_Tmp + 2);
			 TxFrame->Data[3] = *(Velocity_Tmp + 3);
			 TxFrame->Data[4] = 0;
			 TxFrame->Data[5] = 0;
			 TxFrame->Data[6] = 0;
			 TxFrame->Data[7] = 0;
			
			 HAL_FDCAN_AddMessageToTxFifoQ(TxFrame->hcan,&TxFrame->Header,TxFrame->Data);
	 
	 }
	 
	 
}
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

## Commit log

2025-04-01 更新了matlab文件和参考的电机驱动代码
2025-04-01 初步写了电机的控制代码，并增加了2个参考代码
2025-04-01 matlab仿真完成，上传了视频，增加了dm的例程代码
2025-04-03 IMU增加成功，已校准测试，需增加温度闭环进行控制，dwt增加成功，2+2电源开启增加成功，待增加：温控IMU，PS2
2025-04-03 增加了升温控制IMU，并且进行了校准
2025-04-04 没24V电源时测试IMU加热有问题，现在已经修正、校准、并进行了测试，已经具备完整功能。初步实现了PS2控制电机的使能和失能，并成功接收到6个电机的返回值，均已测试完毕。
2025-04-07 之前VMC的问题在于IMU没有完全固定好（之前螺丝长度买错），腿长变化已测试成功，yaw和theta补偿均成功，第一次实现了靠自己站立好
2025-04-11 增加了多项式拟合腿长的m文件，并且能够在命令行生成可直接复制到stm32中直接使用的代码；stm32代码少部分修改，仍然需要先观测好状态变量
2025-04-11 增加了离地检测的计算，增加了kalman计算 机体速度的demo代码
2025-04-11 增加了对pitch角的最小二乘法滤波，后续需要测试该滤波算法的效果并图形化展示
2025-04-11 修正了最小二乘法滤波函数，在CHASSISR中添加了dwt获取系统时间的测试代码，待后续测试
2025-04-11 修正了pitch和dpitch正方向，之前反了
2025-04-14 通过调小v的权重和调小dphi滤波参数，解决了低频抖动问题，在小板凳模式下稳定后上关节也能稳定，其次之前theta补偿写反了，已修正，成功实现了站起来，但目前仍然会向一侧倾倒和有外八问题
2025-04-14 增加了多项式拟合
2025-04-14 初步确立了一个kalman滤波前数据的正方向，编码器是定子和转子之间的相对速度，通过消去定子的转动来获取转子的相对于地面的绝对速度，再通过连杆模型将轮毂的绝对速度转化为机体的绝对速度，最后融合机体绝对速度和加速度计
2025-04-15 多项式拟合成功并测试成功；发现微分项dtheta和dphi不能滤波，否则滞后会产生低频抖动，且其LQR的权重不能过高，否则也会产生抖动；腿长控制测试完成，控位移测试完成，yaw转向控制完成，roll控制完成，且完成了基本参数的调整；初步测试倒地自启的情况，腿会像另一侧摆动，因此倒地自起的时候应该要取消摆腿让Tp=0但应该保留F0的腿长控制收腿，再利用轮毂电机起来，但目前大腿太短倒地倾角过低起来困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
2025-04-24 基本实现所有功能

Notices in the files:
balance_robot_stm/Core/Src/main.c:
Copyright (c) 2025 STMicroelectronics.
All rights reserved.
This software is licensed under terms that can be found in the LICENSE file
